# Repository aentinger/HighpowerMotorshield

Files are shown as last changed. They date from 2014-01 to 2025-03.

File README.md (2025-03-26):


💾 Highpower Motorshield
========================



# 📸 Image

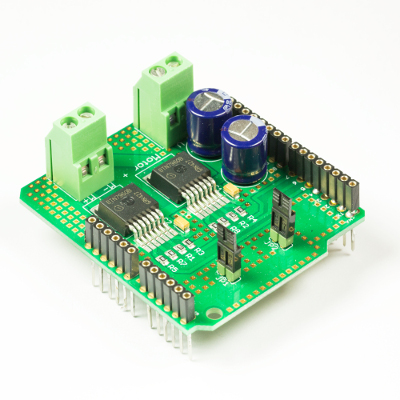
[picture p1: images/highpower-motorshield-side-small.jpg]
LXRobotics P5 HighpowerMotorshield


# 📂 Description

The Highpower Motorshield facilitates the control of a highpower DC (direct current) motor (18 V / 46 A) with an Arduino. The shield also permits the measurement of the motor current. For a quick and easy start, an open source Arduino library with sample programs is available.

**Features**

* Control of a normal direct current motor
* Supply voltage range: 7 to 18 Volts
* Can be used with 2S, 3S and 4S LiPo-battery
* High performance: Maximum continuous output current: 46 A
* Motor drivers are protected against short circuiting (to ground/supply), overheating, overvoltage and undervoltage
* Current measurement of the motor current
* Arduino Library with example programs is available on GitHub

# 🎥 [Video](images/highpower_motorshield_demo.mp4)

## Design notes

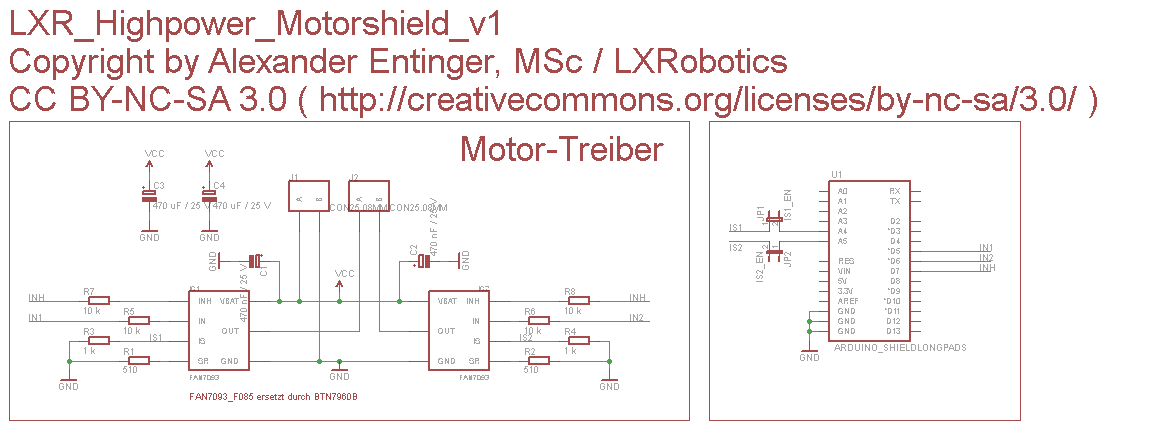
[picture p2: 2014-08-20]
hardware/lxr_highpower_motorshield_v1.png

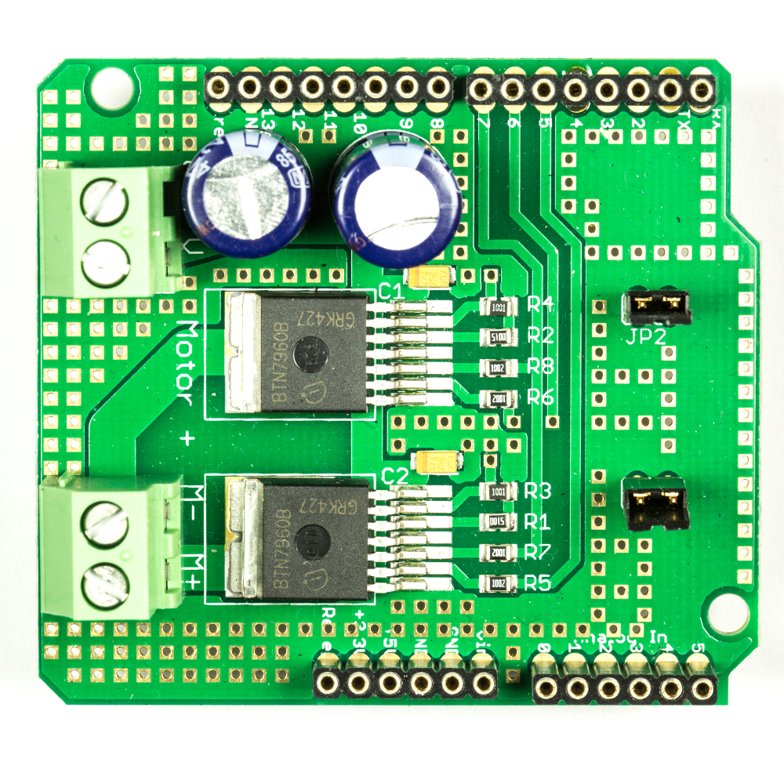
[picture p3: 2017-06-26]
images/highpower-motorshield-top-large.jpg

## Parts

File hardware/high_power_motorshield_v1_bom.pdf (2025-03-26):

Menge | Schaltplan | Bezeichnung | Farnell/Conrad Bestell Nummer | Preis (1 Stück) | Gesamtpreis | Wird bestückt | Footprint | Säckchen
2 | J1, J2 | Schraubklemme 2 Polig | 3041165 | € 1,12 | € 2,24 | | | S1
2 | IC1, IC2 | FAN7093 Leistungshalbbrücke | 2290282 | € | 6,99 | € | 13,98 | x | Bei Farnell aus dem Sortiment genommen, Ersatztyp ist BTN7960B, Digikey-Bauteil-Bezeichnung BTN7960BCT-ND
2 | C1, C2 | KEMET Bauform A, 25 V, 470 nF, Tantal Ko | 1457425 | € | 0,15 | € | 0,30 | x | http://www.digikey.at/product-detail/de/BTN7960B/BTN7960BCT-ND/2231075
2 | C3, C4 | 470 µF, 25 V, Elko, Radial | 1848502 | € 0,37 | € 0,75 | | S2
4 | R5,R6,R7,R8 | 10k, 0805, Widerstand SMD | 1469856 | € 0,02 | € 0,09 | x
2 | R3,R4 | 1k, 0805, Widerstand SMD | 1469847 | € 0,02 | € 0,04 | x
2 | R1,R2 | 510R, 0805, Widerstand SMD | 1653016 | € 0,10 | € 0,20 | x
2 | JP1,JP2 | Stiftleiste, 1 x 2, 2.54 mm, Vertikal, Durchsteck | 3418285 | € 0,24 | € 0,48 | | S3
2 | | Jumper, 2.54 mm, 2 Polig | 4218176 | € 0,14 | € 0,27 | | S3
1 | Satz Arduino Stiftleisten | ELV | € | 0,75 | € | 0,75 | S3 | http://www.elv.at/buchsenleisten-set-fuer-arduino-boards.html
| | | Summe | | € | 19,10

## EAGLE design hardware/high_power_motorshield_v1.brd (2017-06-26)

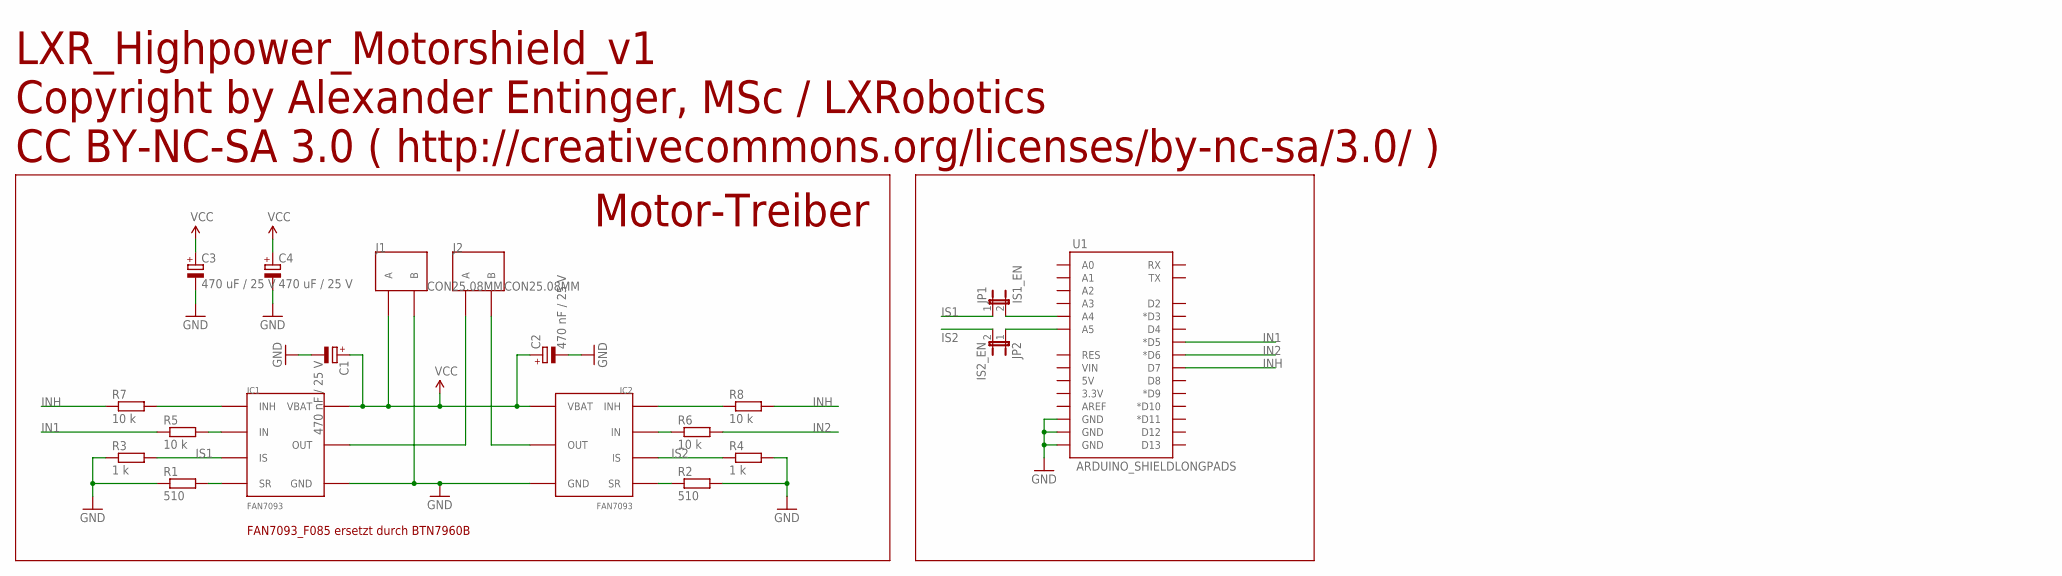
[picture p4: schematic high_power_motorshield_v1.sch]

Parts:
C1, C2: 470 nF / 25 V; KEMET_A
C3, C4: 470 uF / 25 V; E5-10,5
IC1, IC2: FAN7093; TO263-7L
J1, J2: CON25.08MM; CON2_SCHRAUBKLEMME
JP1: IS1_EN; JP1
JP2: IS2_EN; JP1
R1, R2: 510; R0805
R3, R4: 1 k; R0805
R5, R6, R7, R8: 10 k; R0805
U1: ARDUINO_SHIELDLONGPADS; DUEMILANOVE_SHIELD_LONGPADS

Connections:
GND: C1.CATHODE (-), C2.CATHODE (-), C3.-, C4.-, IC1.GND, IC2.GND, J1.2 (B), R1.1, R2.2, R3.1, R4.2, U1.GND@0 (GND), U1.GND@1 (GND), U1.GND@2 (GND)
IN1: R5.1, U1.D5 (*D5)
IN2: R6.2, U1.D6 (*D6)
INH: R7.1, R8.2, U1.D7
IS1: IC1.IS, JP1.1, R3.2
IS2: IC2.IS, JP2.2, R4.1
unnamed: IC1.INH, R7.2
unnamed: IC1.IN, R5.2
unnamed: IC1.OUT, IC1.OUT@1 (OUT), J2.1 (A)
unnamed: IC2.OUT, IC2.OUT@1 (OUT), J2.2 (B)
unnamed: JP1.2, U1.A4
unnamed: IC1.SR, R1.2
unnamed: IC2.SR, R2.1
unnamed: JP2.1, U1.A5
unnamed: IC2.IN, R6.1
unnamed: IC2.INH, R8.1
VCC: C1.ANODE (+), C2.ANODE (+), C3.+, C4.+, IC1.VBATT (VBAT), IC2.VBATT (VBAT), J1.1 (A)

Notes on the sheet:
LXR_Highpower_Motorshield_v1 Copyright by Alexander Entinger, MSc / LXRobotics CC BY-NC-SA 3.0 ( http://creativecommons.org/licenses/by-nc-sa/3.0/ )
Motor-Treiber
FAN7093_F085 ersetzt durch BTN7960B

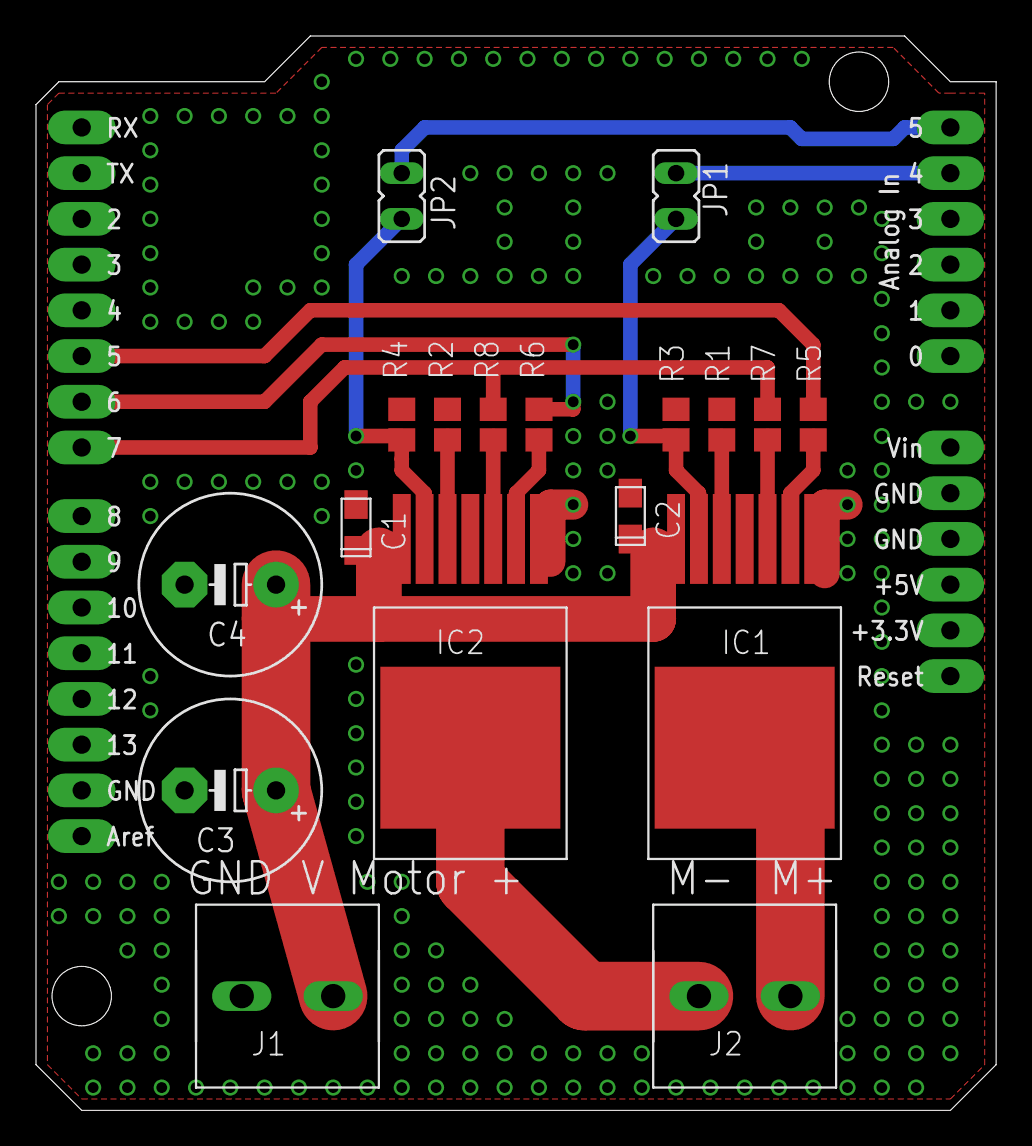
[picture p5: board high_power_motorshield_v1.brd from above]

Board: 2 copper layers, 53.3 x 59.7 mm, 19 parts (0 on the bottom side), 17 nets.

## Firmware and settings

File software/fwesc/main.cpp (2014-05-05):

/** 
 * @author Alexander Entinger, MSc / LXRobotics
 * @brief main file for lxrobotics highpower motorshield featherweight electronic speed controller
 * @file main.cpp
 * @license CC BY-NC-SA 3.0 ( http://creativecommons.org/licenses/by-nc-sa/3.0/ )
 */

/* INCLUDE SECTION */
#include "motor.h"
#include "input.h"
#include "control.h"
#include "adc.h"
#include <avr/interrupt.h>

/* PROTOTYPE SECTION */
void init_application();

/* FUNCTION SECTION */

int main(void) {
    
	init_application();
	
	for(;;) {
		if(control::is_runnable()) {
			control::run();
		}
	}
}

/** 
 * @brief initializes the application
 */
void init_application() {
	
	// initialize the motor module
	motor::init();
	
	// initialize the input module
	input::init();
	
	// initialize the adc module
	adc::init();
	
	// globally enable interrupts
	sei();
}

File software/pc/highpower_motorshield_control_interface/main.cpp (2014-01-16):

/* This Source Code Form is subject to the terms of the Mozilla Public
 * License, v. 2.0. If a copy of the MPL was not distributed with this
 * file, You can obtain one at http://mozilla.org/MPL/2.0/. */

/**
 * @author Alexander Entinger, MSc
 * @brief main file for highpower motor controller
 * @file main.cpp
 * @license MPL 2.0
 */

#include <iostream>
#include <cstdlib>

#include "lxr_hp_motor_control.h"

/**
 * @brief error handler function
 */
void error_handler(size_t const err_code) {
	std::cout << lxr_hp_motor_control::convert_to_string(err_code);
	exit(1);
}

int main(int argc, char **argv) {

	unsigned char const serial_motor_driver_id = 128;

	lxr_hp_motor_control mc("/dev/ttyACM0", serial_motor_driver_id);
	mc.register_error_callback(&error_handler);

	char cmd = 0;
	do {
		std::cout << "LXRobotics Highpower Motorshield Control Menu" << std::endl << std::endl;
		std::cout << "[0]\tset speed" << std::endl;
		std::cout << "[1]\tset direction" << std::endl;
		std::cout << "[q]\tquit" << std::endl;
		std::cout << ">> "; std::cin >> cmd;

		switch(cmd) {
		case '0': {
			size_t speed = 0;
			std::cout << "Enter speed" << std::endl << ">> ";
			std::cin >> speed;
			if(speed > 255) {
				std::cout << "Error, speed is in range of 0 to 255" << std::endl;
			} else {
				mc.set_speed(static_cast<unsigned char>(speed));
			}
		} break;
		case '1': {
			char dir = 0;
			std::cout << "Select direction" << std::endl;
			std::cout << "[0]\tFWD" << std::endl;
			std::cout << "[1]\tBWD" << std::endl << ">> " << std::endl;
			std::cin >> dir;
			switch(dir) {
			case '0': mc.set_direction(E_FWD); break;
			case '1': mc.set_direction(E_BWD); break;
			default: std::cout << "Error, only 0 and 1 are possible selections" << std::endl; break;
			}
		} break;
		case 'q': {
			std::cout << "Exiting now." << std::endl;
		} break;
		default: {
			std::cout << "Wrong command, try again" << std::endl;
		} break;
		}

	} while(cmd != 'q');

	return EXIT_SUCCESS;
}

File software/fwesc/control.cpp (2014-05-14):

/**
* @author Alexander Entinger, MSc / LXRobotics
* @brief this moduls maps the receiver pulse width to an appropriate motor action
* @file control.cpp
* @license CC BY-NC-SA 3.0 ( http://creativecommons.org/licenses/by-nc-sa/3.0/ )
*/

#include "control.h"
#include "motor.h"
#include "linear_mapper.h"
#include "defines.h"

#include <avr/interrupt.h>
#include <avr/io.h>

/* GLOBAL CONSTANT SECTION */
static uint8_t const DEADZONE = 20;
static uint16_t const CH1_PULSE_WIDTH_MIN_US = 1120;
static uint16_t const CH1_PULSE_WIDTH_MAX_US = 1910;
static uint16_t const CH2_PULSE_WIDTH_MIN_US = 1120;
static uint16_t const CH2_PULSE_WIDTH_MAX_US = 1910;

/* TYPEDEF SECTION */
typedef struct {
	uint16_t pulse_width_us;
	uint16_t neutral_pulse_width_us;
	uint16_t deadzone;
	bool is_updated;
} s_channel;

typedef struct {
	bool calibration_complete;
} s_control_data;

/* GLOBAL VARIABLE SECTION */
static s_channel m_channel_1 = {1500, 1500, DEADZONE, false};
static s_channel m_channel_2 = {1500, 1500, DEADZONE, false};
static s_control_data m_control_data = {false};

// the mappers map the channel input to motor speed values
static linear_mapper m_mapper_1_channel_1(CH1_PULSE_WIDTH_MIN_US, m_channel_1.neutral_pulse_width_us, (-1)*(1<<14), 0);
static linear_mapper m_mapper_2_channel_1(m_channel_1.neutral_pulse_width_us, CH1_PULSE_WIDTH_MAX_US, 0, (1<<14));
static linear_mapper m_mapper_1_channel_2(CH2_PULSE_WIDTH_MIN_US, m_channel_2.neutral_pulse_width_us, (-1)*(1<<14), 0);
static linear_mapper m_mapper_2_channel_2(m_channel_2.neutral_pulse_width_us, CH2_PULSE_WIDTH_MAX_US, 0, (1<<14));

/* PROTOTYPE SECTION */
int16_t abs(int16_t const val);
void calibrate();
void sort(uint16_t *data, uint8_t const length);
void swap(uint16_t *elem1, uint16_t *elem2);
uint16_t median(uint16_t const *data, uint8_t const length);


/* FUNCTION SECTION */

/**
* @brief updates channel 1 - only to be called within isr context
*/
void control::update_channel_1(uint16_t const ch1_pulse_width_us) {
	m_channel_1.pulse_width_us = ch1_pulse_width_us;
	m_channel_1.is_updated = true;
}

/**
* @brief updates channel 2 - only to be called within isr context
*/
void control::update_channel_2(uint16_t const ch2_pulse_width_us) {
	m_channel_2.pulse_width_us = ch2_pulse_width_us;
	m_channel_2.is_updated = true;
}

/**
* @brief this function is called by the input module to indicate that channels have been lost - only to be called within isr context
*/
void control::channel_s_lost() {
	motor::set_direction(BREAK);
	motor::set_speed(0);
	m_channel_1.is_updated = false;
	m_channel_2.is_updated = false;
}


/**
* @brief the control task itself - it is scheduled to be runnable after both channels have updated their data value
*/
void control::run() {
	
	if(m_control_data.calibration_complete) {
		
		// calibration is complete, perform the control
		
		// ch1 is forward/backward
		// ch2 is left/right
		
		int16_t ch1_motor_value = 0, ch2_motor_value = 0;
		
		// perform the mapping and correct the result by shifting 6 right -> resulting area is between -255 and +255
		if(m_channel_1.pulse_width_us < m_channel_1.neutral_pulse_width_us) {
			ch1_motor_value = (m_mapper_1_channel_1.map((int16_t)(m_channel_1.pulse_width_us)) / (1<<6));
		} else if(m_channel_1.pulse_width_us > m_channel_1.neutral_pulse_width_us) {
			ch1_motor_value = (m_mapper_2_channel_1.map((int16_t)(m_channel_1.pulse_width_us)) / (1<<6));
		} else {
			ch1_motor_value = 0;
		}
		if(m_channel_2.pulse_width_us < m_channel_2.neutral_pulse_width_us) {
			ch2_motor_value = (m_mapper_1_channel_2.map((int16_t)(m_channel_2.pulse_width_us)) / (1<<6));
		} else if(m_channel_2.pulse_width_us > m_channel_2.neutral_pulse_width_us) {
			ch2_motor_value = (m_mapper_2_channel_2.map((int16_t)(m_channel_2.pulse_width_us)) / (1<<6));
		} else {
			ch2_motor_value = 0;
		}
		
		// simple delta mixing
#ifdef RIGHT_MOTOR
		ch1_motor_value += ch2_motor_value;
#endif
#ifdef LEFT_MOTOR
		ch1_motor_value -= ch2_motor_value;
#endif
		
		// limit to +/- 255
		if(ch1_motor_value > 255) ch1_motor_value = 255;
		if(ch1_motor_value < -255) ch1_motor_value = -255;
		
		if(ch1_motor_value >= 0) {
			if((uint16_t)(ch1_motor_value) > m_channel_1.deadzone) {
				motor::set_speed((uint8_t)(ch1_motor_value));
				motor::set_direction(FORWARD);
			} else {
				motor::set_speed(0);
				motor::set_direction(BREAK);
			}
		} else {
			ch1_motor_value = abs(ch1_motor_value);
			if((uint16_t)(ch1_motor_value) > m_channel_1.deadzone) {
				motor::set_speed((uint8_t)(ch1_motor_value));
				motor::set_direction(BACKWARD);
			} else {
				motor::set_speed(0);
				motor::set_direction(BREAK);
			}
		}
	} else {
		// do the calibration
		calibrate();
	}

	// task has been executed, clear the runnable flags
	cli();
	m_channel_1.is_updated = false;
	m_channel_2.is_updated = false;
	sei();
}

/**
* @brief returns true if the control task is runnable in the main thread
*/
bool control::is_runnable() {
	cli();
	bool const runnable = (m_channel_1.is_updated && m_channel_2.is_updated);
	sei();
	return runnable;
}

/**
* @brief returns |val|
*/
int16_t abs(int16_t const val) {
	int16_t res = 0;
	val < 0 ? res = (0 - val) : res = val;
	return res;
}

/** 
 * @brief performs the calibration
 */
void calibrate() {
	// here we store the first 16 values of both channels in an array, drop the 2 highest and the 2 lowest values and get the average
	uint8_t const MAX_RECEIVED_PULSES = 16;
	static uint8_t received_pulses_cnt = 0;
	static uint16_t ch1[16] = {0};
	static uint16_t ch2[16] = {0};
	// insert received values into the channel arrays
	ch1[received_pulses_cnt] = m_channel_1.pulse_width_us;
	ch2[received_pulses_cnt] = m_channel_2.pulse_width_us;
	// update the cnt
	received_pulses_cnt++;
	if(received_pulses_cnt >= MAX_RECEIVED_PULSES) {
		// sort
		sort(ch1, MAX_RECEIVED_PULSES);
		sort(ch2, MAX_RECEIVED_PULSES);
		// drop the two lowest and highest values and average
		m_channel_1.neutral_pulse_width_us = median(ch1 + 2, MAX_RECEIVED_PULSES - 4);
		m_channel_2.neutral_pulse_width_us = median(ch2 + 2, MAX_RECEIVED_PULSES - 4);
		// recalibrate the linear mappers
		m_mapper_1_channel_1.init(CH1_PULSE_WIDTH_MIN_US, m_channel_1.neutral_pulse_width_us, (-1)*(1<<14), 0);
		m_mapper_2_channel_1.init(m_channel_1.neutral_pulse_width_us, CH1_PULSE_WIDTH_MAX_US, 0, (1<<14));
		m_mapper_1_channel_2.init(CH2_PULSE_WIDTH_MIN_US, m_channel_2.neutral_pulse_width_us, (-1)*(1<<14), 0);
		m_mapper_2_channel_2.init(m_channel_2.neutral_pulse_width_us, CH2_PULSE_WIDTH_MAX_US, 0, (1<<14));
		// update the calibration complete flag
		m_control_data.calibration_complete = true;
	}
}

/** 
 * @brief sorts the array ascending
 */
void sort(uint16_t *data, uint8_t const length) {
	bool elements_swapped = false;
	do {
		elements_swapped = false;
		uint8_t i=1; for(; i<length; i++) {
			if(data[i-1] > data[i]) {
				swap(&data[i-1], &data[i]);
				elements_swapped = true;
			}
		}		
	} while(elements_swapped);
}
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

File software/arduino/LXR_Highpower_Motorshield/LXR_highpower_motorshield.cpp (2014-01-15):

/**
 * @author Alexander Entinger, MSc / LXRobotics
 * @brief this module implements the control of the LXRobotics Highpower Arduino Motorshield
 * @file LXR_highpower_motorshield.cpp
 * @license CC BY-NC-SA 3.0 ( http://creativecommons.org/licenses/by-nc-sa/3.0/ )
 */

#include "LXR_highpower_motorshield.h"

#include <avr/io.h>
#include <avr/interrupt.h>
#include <Arduino.h>

// IN1 = D5 = PD5 = OC0B
#define IN1_DDR		(DDRD)
#define IN1_PORT	(PORTD)
#define IN1		(1<<5)
// IN2 = D6 = PD6 = OC0A
#define IN2_DDR		(DDRD)
#define IN2_PORT	(PORTD)
#define IN2		(1<<6)
// INH = D7 = PD7
#define INH_DDR		(DDRD)
#define INH_PORT	(PORTD)
#define INH		(1<<7)
// IS1 = A4
#define IS1             (4)
// IS1 = A4
#define IS2             (5)

typedef struct {
  uint8_t spd;
  E_DIRECTION dir;
} 
s_motor_params;
static volatile s_motor_params m_motor_params = {
  0, FWD};

/**
 * @brief initializes the motorshield
 */
void LXR_highpower_motorshield::begin() {
  // set inh to output and to low (halfbridges deactivated)
  INH_PORT &= ~INH;
  INH_DDR |= INH;
  // set inX pins to outputs with value low
  IN1_PORT &= ~IN1;
  IN1_DDR |= IN1;
  IN2_PORT &= ~IN2;
  IN2_DDR |= IN2;
  // clear TCCR2A from whatever might be still left there
  TCCR2A = 0x00;	
  // reset the timer value
  TCNT2 = 0;
  // enable compare and overflow interrupts
  TIMSK2 = (1<<OCIE2A) | (1<<TOIE2);
  // activate timer with prescaler 32 => f_PWM = 1,96 kHz
  TCCR2B = (1<<CS21) | (1<<CS20);
  // set direction
  LXR_highpower_motorshield::set_direction(m_motor_params.dir);
  // set speed
  LXR_highpower_motorshield::set_speed(m_motor_params.spd);
  // activate h brigde
  INH_PORT |= INH;
}

/** 
 * @brief set the speed of the motor control
 * @param speed 0 => 0 speed, 255 => max speed
 */
void LXR_highpower_motorshield::set_speed(uint8_t const speed) {
  m_motor_params.spd = speed;
  OCR2A = m_motor_params.spd;
}

/** 
 * @brief returns the current motor speed
 */
uint8_t LXR_highpower_motorshield::get_speed() {
  return m_motor_params.spd;
}

/** 
 * @brief sets the direction of the motor
 * @param dir direction
 */
void LXR_highpower_motorshield::set_direction(E_DIRECTION const dir) {
  m_motor_params.dir = dir;
}

/** 
 * @brief returns the current direction
 */
E_DIRECTION LXR_highpower_motorshield::get_direction() {
  return m_motor_params.dir;
}

/**
 * @brief returns the current flow over the half brigde 1
 */
int LXR_highpower_motorshield::get_current_half_brigde_1() {
  return analogRead(IS1);
}

/**
 * @brief returns the current flow over the half brigde 2
 */
int LXR_highpower_motorshield::get_current_half_brigde_2() {
  return analogRead(IS2);
}

/**
 * @brief ISR for timer 2 overflow
 */
ISR(TIMER2_OVF_vect) {
  if(m_motor_params.spd > 0) {
    if(m_motor_params.dir == FWD) IN1_PORT |= IN1;
    else if(m_motor_params.dir == BWD) IN2_PORT |= IN2;
  }
}

/**
 * @brief ISR for compare a interrupt
 */
ISR(TIMER2_COMPA_vect) {
  IN1_PORT &= ~IN1;	
  IN2_PORT &= ~IN2;
}

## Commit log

2014-01-15 initial checkin of highpower motorshield
2014-01-16 adding software for driving motor via serial interface
2014-01-16 minor change in serial motor driver (activating timeout)
2017-06-26 Adding hardware and images
    [high_power_motorshield_v1.brd, high_power_motorshield_v1.sch]
2025-03-26 Add BOM.

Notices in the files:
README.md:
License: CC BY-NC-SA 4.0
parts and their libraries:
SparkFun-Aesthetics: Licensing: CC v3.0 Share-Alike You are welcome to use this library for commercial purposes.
